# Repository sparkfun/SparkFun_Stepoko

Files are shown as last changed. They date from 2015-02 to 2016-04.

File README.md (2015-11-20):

SparkFun GRBL Board
========================================

SparkFun Stepoko

[*SparkFun Stepoko (ROB-13155)*](https://www.sparkfun.com/products/13155)

A 3 axis motor controller for use with grbl.

Repository Contents (template)
-------------------

* **/Examples** - Example gcode files, projects, and settings
* **/Hardware** - Eagle design files (.brd, .sch)
* **/Mechanical** - Enclosure and heatsink mechanical drawings
* **/Production** - Production panel files (.brd)

Documentation
--------------
* **Hookup Guide** - Basic hookup guide for the Stepoko
* **Coaster Project Tutorial** - Process of creating the coaster example
* **[SparkFun Fritzing repo](https://github.com/sparkfun/Fritzing_Parts)** - Fritzing diagrams for SparkFun products.
* **[SparkFun 3D Model repo](https://github.com/sparkfun/3D_Models)** - 3D models of SparkFun products. 

Product Versions
----------------
[*SparkFun Stepoko (ROB-13155)*](https://www.sparkfun.com/products/13155)

Version History
---------------
* [v1.0](https://github.com/sparkfun/SparkFun_Stepoko/tree/V_1_0) - Released to Reds
* [v1.1](https://github.com/sparkfun/SparkFun_Stepoko/tree/V_1_1) - Changed pot symbol name and 'top-side' resistor value
* [v1.2](https://github.com/sparkfun/SparkFun_Stepoko/tree/V_1_2) - Updated capacitor values, documentation finished

License Information
-------------------

This product is _**open source**_! 

Please review the LICENSE.md file for license information. 

If you have any questions or concerns on licensing, please contact techsupport@sparkfun.com.

Distributed as-is; no warranty is given.

- Your friends at SparkFun.

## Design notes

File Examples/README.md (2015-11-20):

Stepoko Examples
========================================

This directory contains example 3D models, machine code, and settings

Directory Contents
-------------------

* **/BasicShapes** - Example gcode files that drive the mill in 10 inch squares and lines at various speeds
* **/FlameCoaster** - Flat design files and gcode exports for cutting and engraving a SparkFun coaster.
* **/grblSettings** - Example settings for the grbl software; stock Shapeoko, fast Shapeoko, and CDrom steppers.
* **/MidiShieldEnclosure** - 3D models and mill paths to cut a wood enclosure and panel top.

License Information
-------------------

This product is _**open source**_! 

Please review the LICENSE.md file for license information. 

If you have any questions or concerns on licensing, please contact techsupport@sparkfun.com.

Distributed as-is; no warranty is given.

- Your friends at SparkFun.

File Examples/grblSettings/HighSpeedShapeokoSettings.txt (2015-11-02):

(New settings)
$0=30 (step pulse, usec)
$1=255 (step idle delay, msec)
$2=0 (step port invert mask:00000000)
$3=0 (dir port invert mask:00000000)
$4=0 (step enable invert, bool)
$5=0 (limit pins invert, bool)
$6=0 (probe pin invert, bool)
$10=3 (status report mask:00000011)
$11=0.050 (junction deviation, mm)
$12=0.002 (arc tolerance, mm - NEW SETTING)
$13=0 (report inches, bool)
$20=0 (soft limits, bool)
$21=0 (hard limits, bool)
$22=0 (homing cycle, bool)
$23=1 (homing dir invert mask:00000001)
$24=25.000 (homing feed, mm/min)
$25=250.000 (homing seek, mm/min)
$26=100 (homing debounce, msec)
$27=1.000 (homing pull-off, mm)
$100=40 (x, step/mm)
$101=40 (y, step/mm)
$102=40 (z, step/mm)
$110=10000.000 (x max rate, mm/min)
$111=10000.000 (y max rate, mm/min)
$112=1000.000 (z max rate, mm/min)
$120=100.000 (x accel, mm/sec^2)
$121=100.000 (y accel, mm/sec^2)
$122=100.000 (z accel, mm/sec^2)

$130=500.000 (x max travel, mm - NEW SETTING)
$131=500.000 (y max travel, mm - NEW SETTING)
$132=30.000 (z max travel, mm - NEW SETTING)

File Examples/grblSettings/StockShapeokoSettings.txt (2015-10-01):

(New settings)
$0=30 (step pulse, usec)
$1=255 (step idle delay, msec)
$2=0 (step port invert mask:00000000)
$3=0 (dir port invert mask:00000000)
$4=0 (step enable invert, bool)
$5=0 (limit pins invert, bool)
$6=0 (probe pin invert, bool)
$10=3 (status report mask:00000011)
$11=0.050 (junction deviation, mm)
$12=0.002 (arc tolerance, mm - NEW SETTING)
$13=0 (report inches, bool)
$20=0 (soft limits, bool)
$21=0 (hard limits, bool)
$22=0 (homing cycle, bool)
$23=1 (homing dir invert mask:00000001)
$24=25.000 (homing feed, mm/min)
$25=250.000 (homing seek, mm/min)
$26=100 (homing debounce, msec)
$27=1.000 (homing pull-off, mm)
$100=40 (x, step/mm)
$101=40 (y, step/mm)
$102=40 (z, step/mm)
$110=500.000 (x max rate, mm/min)
$111=500.000 (y max rate, mm/min)
$112=500.000 (z max rate, mm/min)
$120=25.000 (x accel, mm/sec^2)
$121=25.000 (y accel, mm/sec^2)
$122=25.000 (z accel, mm/sec^2)
$130=225.000 (x max travel, mm - NEW SETTING)
$131=125.000 (y max travel, mm - NEW SETTING)
$132=170.000 (z max travel, mm - NEW SETTING)

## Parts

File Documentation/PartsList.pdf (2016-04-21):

Deluxe Shapeoko Parts List | Approximate Sizes
Check | Qty. Item description | Metric | Inches
Large:
2 | Waste-boards | 58x36cm | 22x14in
2 | long extrusions/rails, no tap holes | 60cm | 24in
1 | long extrusion/rails, two tapped holes | 60cm | 24in

Red Plates:
2 | “L” shaped base ends | 72cm | 28in
1 | “I” shape (Cross strap, for sub base) | 68cm | 27in
1 | center strap, 4 slotted holes | 58cm | 22in
2 | side strap, 2 holes | 58cm | 22in
1 | moving Z axis plate, 2 tabs | 18x16cm | 7x6in
1 | 25x17cm | 10x7in
2 | 21x16cm | 8x6in

Electronics:
4 | Wantai stepper motors (NEMA 23)
1 | 1x Stepoko controller board
1 | 1x usb cable
1 | 1x SPST toggle
1 | 1x IEC power cord, US
1 | 1x power supply brick

Misc HW:
1 | 1DPN611 spindle mount | 10x9x3cm | 4x4x1in
2 | extrusions with 45deg rail, z axis rails | 20x2x2.7cm 8x1x1in
1 | red plastic enclosure with pre-milled holes
1 | red plastic enclosure lid
1 | Shapeoko placard
2 | expansion springs | 5.5cm | 2in
6 | Belt clips, angle with two slots and two holes
10 | 3M Bump-on rubber bumpers
1 | 10mm open end wrench
1 | 8mm open end wrench
1 | 13mm open end wrench
5 | Allen hex keys
1 | Tube thread-locker (jet-lube branding)
1 | Sharpie
1 | Thermal gap filler pad | 7.5x10cm | 3x4 in
3 | cable carriers | 1x1.5x50cm ~20 in

Spacers and Stand-Offs:
2 | 10-24 x 1 inch, threaded | 2.5cm | 1in
4 | 9mm O.D, 1-1/4 inch long | 1 ¼ in
4 | 3/8in O.D., .219in I.D, by 3/8in | 3/8 in
1 | 3/8in O.D., .219in I.D,by 5/16in | 5/16 in
2 | M5 x 15mm threaded | 1.5cm | 0.6 in
6 | 0.5in O.D., 0.319 I.D, x10mm | 1cm | 0.4 in

fixed Z axis plate (moves with Y axis), centered large motor hole
Y axis end plates, offset motor hole. (Moves with X axis)

Belts:
3 | Split belts (GT2, 800mm) | 80cm | 31.5 in
1 | Continuous belt (GT2, 524mm) | 52.4cm | 20.6 in

Pulleys:
4 | 6.3mm bore (GT2 profile)
1 | 5mm bore (GT2 profile)
10 | (or more) set screws for pulleys

Bolts/screws:
6 | M8 x 35mm | 35mm | 1.4 in
30 | M6 x 12mm | 12mm | 0.47 in
1 | M6 x 30mm | 30mm | 1.2 in
25 | M5 x 16mm | 16mm | 0.63 in
22 | M5 x 20mm | 20mm | 0.79 in
2 | M5 x 55, cylindrical hex cap (SHCS) | 55mm | 2.16 in
4 | M5 x 40mm | 40mm | 1.6 in
1 | M5 x 25mm | 25mm | 1 in
2 | 10-24 thread, 3/4inch | 19mm | 0.75 in
12 | M3 x 12mm gnarled hex cap (SHCS) | 12mm | 0.5 in
6 | 6-32 x 3/4in for red enclosure lid | 19mm | 0.75 in
8 | 4-40 x 3/8in for PCB mounting | 9mm | 0.375 in

Nuts:
6 | M8 Hex Nut
1 | M6 x 6mm Hex Nut
4 | M6 Square Nut
29 | M5 Hex Nut
8 | Hex Nut with eccentric hole and shoulder
12 | M3 Hex Nut

Washers:
4 | M6 Flat Washer
18 | M5 Flat Washer

Bearings:
16 | Black V-guide pulleys
12 | 25mm outside diameter(8x22x7mm) | 1 in
2 | 14mm outside diameter (6mm flanged bearing) | 0.5 in

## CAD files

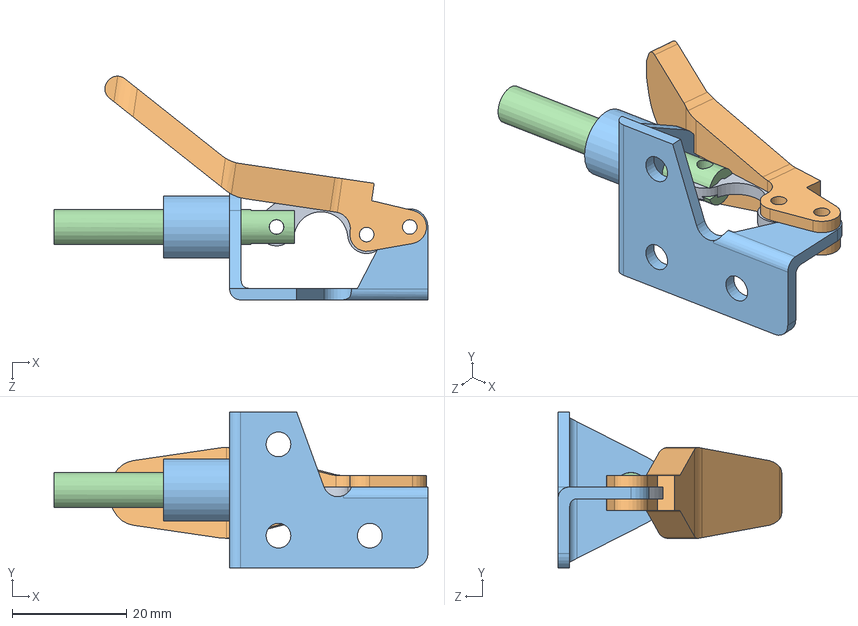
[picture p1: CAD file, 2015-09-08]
Mechanical/HeatsinkJig/ToggleClamp.SLDASM
65.1 x 27.2 x 39.0 mm
ToggleClampConnector
ToggleClampLever
toggleClampMount
ToggleClampPlunger

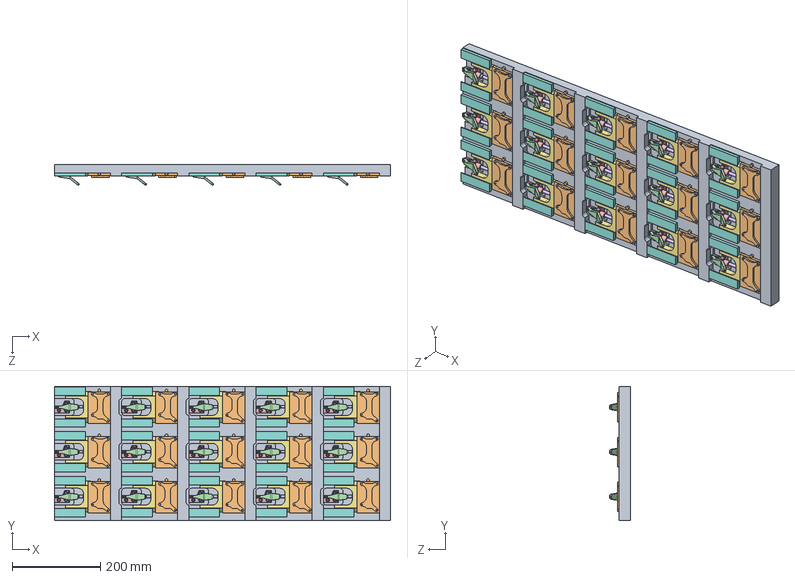
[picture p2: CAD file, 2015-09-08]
Mechanical/HeatsinkJig/HeatSinkJig.SLDASM
762.0 x 304.8 x 46.6 mm
JigBase
HeatSink x 15
ToggleClampConnector x 15
ToggleClampLever x 15
toggleClampMount x 15
ToggleClampPlunger x 15
JigClampFace x 15
dovetail x 30
socket head cap screw_ai x 46
rollpin x 15

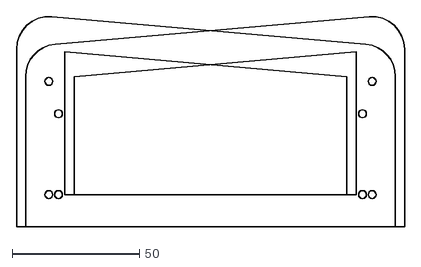
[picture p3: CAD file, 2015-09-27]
Examples/MidiShieldEnclosure/Controlled/dxf/SideParts.dxf
152.4 x 82.8

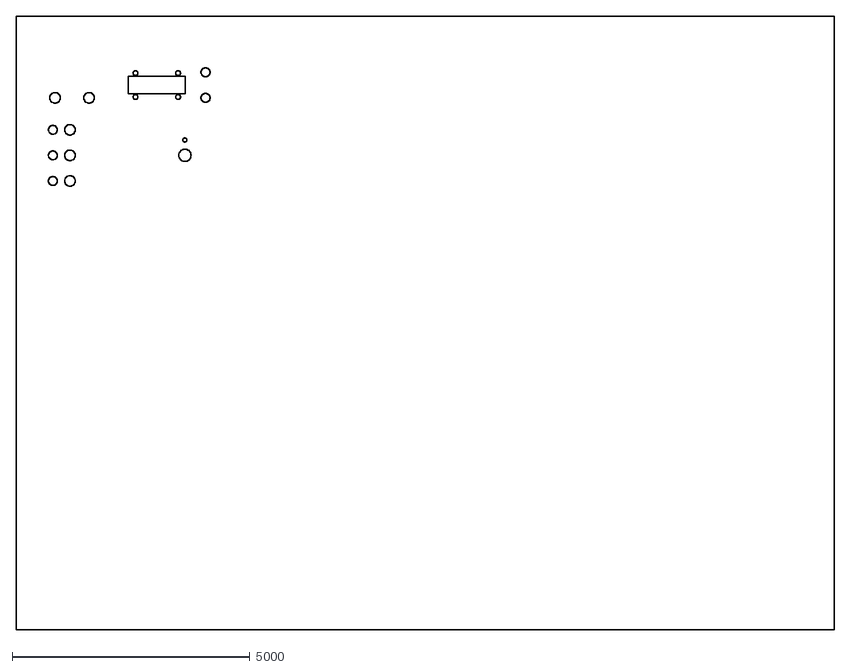
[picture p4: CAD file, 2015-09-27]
Examples/MidiShieldEnclosure/PanelExports/panel_holes.dxf
17204.3 x 12903.2

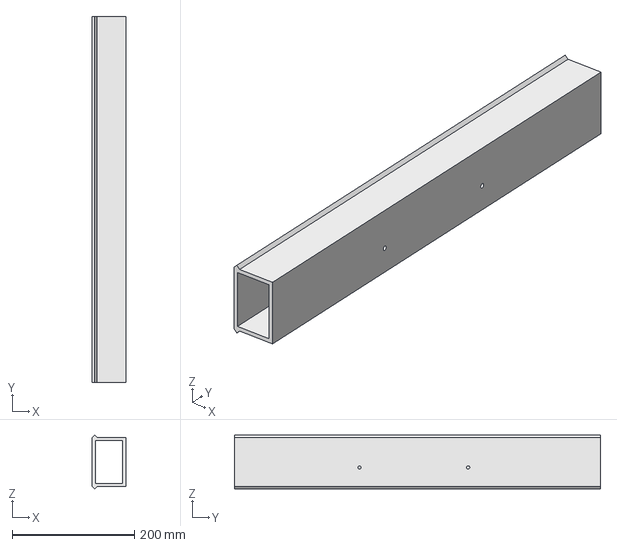
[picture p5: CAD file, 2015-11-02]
Mechanical/ChassisMount/RailPart.FCStd
55.0 x 600.0 x 88.0 mm

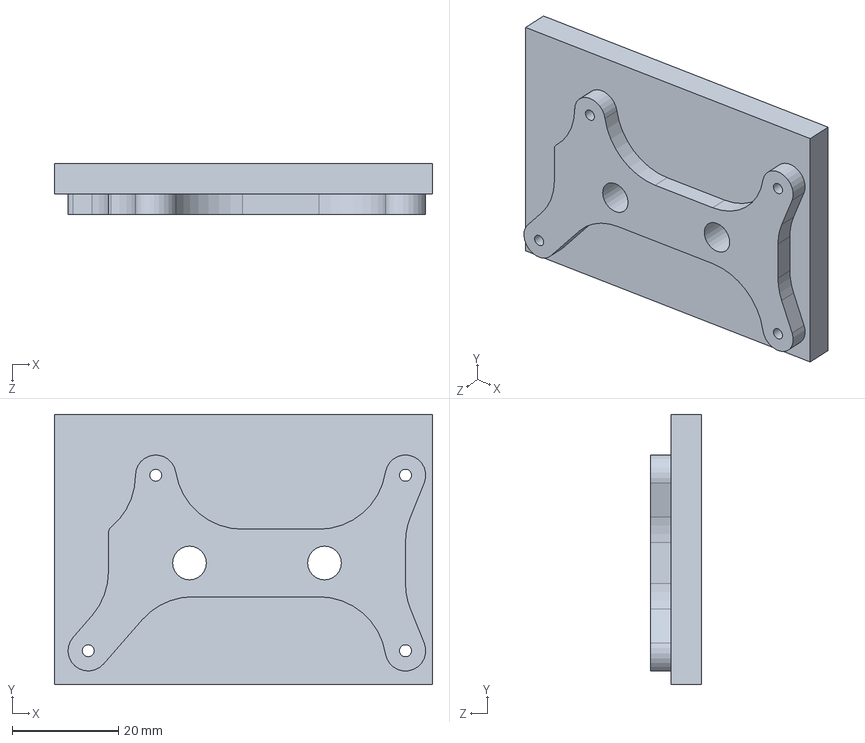
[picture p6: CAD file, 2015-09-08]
Mechanical/HeatSink.SLDPRT
71.1 x 50.8 x 9.53 mm

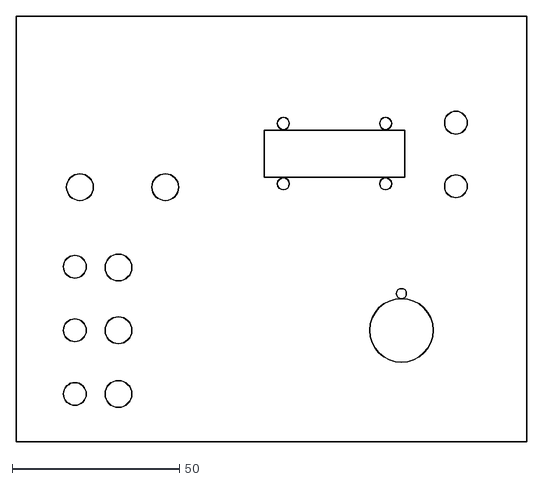
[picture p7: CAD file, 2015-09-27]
Examples/MidiShieldEnclosure/PanelExports/freecadexport.dxf
152.4 x 127.0

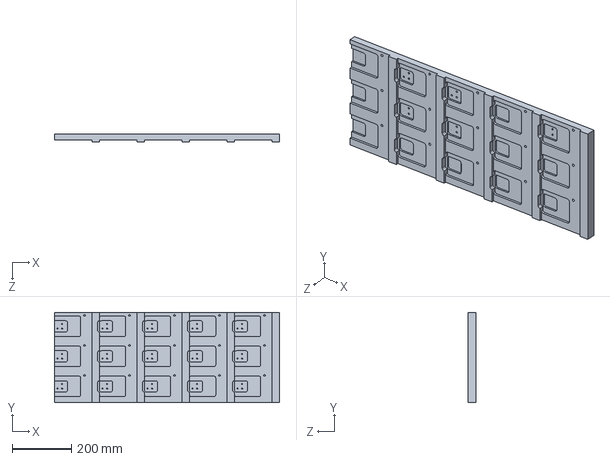
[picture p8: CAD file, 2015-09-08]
Mechanical/HeatsinkJig/JigBase.SLDPRT
762.0 x 304.8 x 25.4 mm

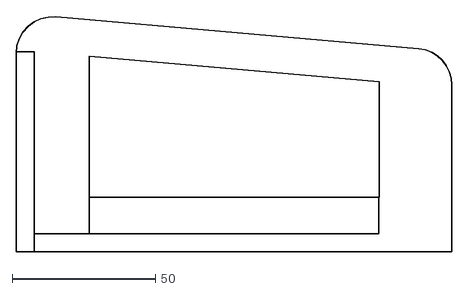
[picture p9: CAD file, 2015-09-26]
Examples/MidiShieldEnclosure/PanelTestMaster.dxf
151.9 x 82.3

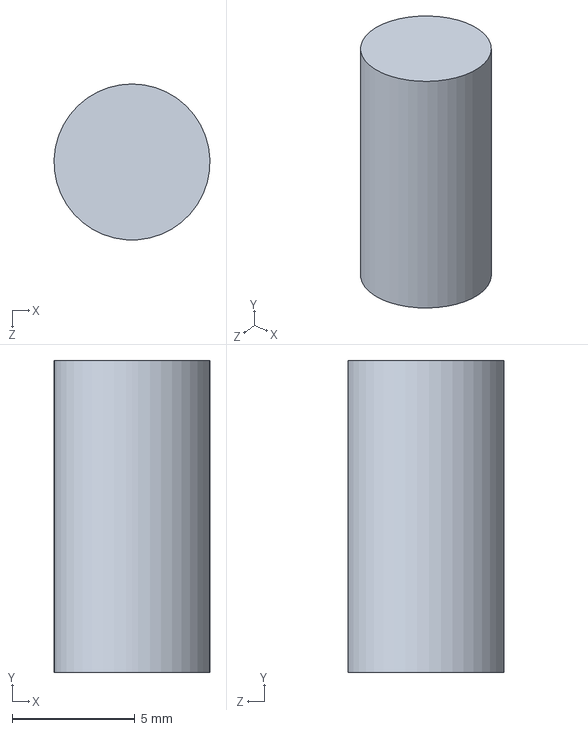
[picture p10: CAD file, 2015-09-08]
Mechanical/HeatsinkJig/rollpin.SLDPRT
6.35 x 12.7 x 6.35 mm

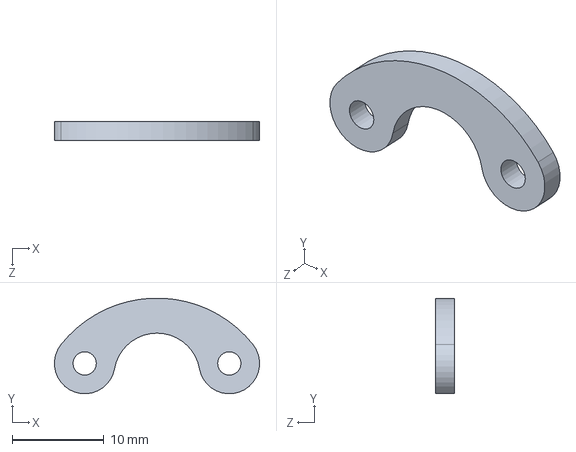
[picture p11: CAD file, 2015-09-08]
Mechanical/HeatsinkJig/ToggleClampConnector.SLDPRT
22.3 x 10.4 x 2.03 mm

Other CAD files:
Examples/MidiShieldEnclosure/Components.FCStd
Examples/MidiShieldEnclosure/Controlled/FrontPart.FCStd
Examples/MidiShieldEnclosure/Controlled/PanelPart.FCStd
Examples/MidiShieldEnclosure/TopPanel.FCStd
Examples/MidiShieldEnclosure/Controlled/BottomPart.FCStd
Examples/MidiShieldEnclosure/Controlled/BackPart.FCStd
Examples/MidiShieldEnclosure/Controlled/SideView.FCStd
Examples/MidiShieldEnclosure/Controlled/dxf/BackPart.dxf
Examples/MidiShieldEnclosure/Controlled/dxf/BottomPart.dxf
Examples/MidiShieldEnclosure/Controlled/dxf/FrontPart.dxf
Examples/MidiShieldEnclosure/Controlled/dxf/PanelPart.dxf
Mechanical/HeatsinkJig/JigClampFace.SLDPRT
Mechanical/HeatsinkJig/ToggleClampLever.SLDPRT
Mechanical/HeatsinkJig/ToggleClampPlunger.SLDPRT
Mechanical/HeatsinkJig/dovetail.SLDPRT
Mechanical/HeatsinkJig/toggleClampMount.SLDPRT

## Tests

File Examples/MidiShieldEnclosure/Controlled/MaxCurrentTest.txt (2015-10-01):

10,23.50,24.25,24.00,23.50
15,23.50,24.25,24.25,23.50
20,23.50,24.50,24.25,23.50
25,23.50,24.25,24.00,23.50
30,23.50,24.25,24.00,23.50
35,23.50,24.25,24.00,23.75
40,23.50,24.25,24.00,23.75
45,23.50,24.25,24.00,23.50
50,23.50,24.25,24.00,23.50
55,23.50,24.25,24.00,23.50
60,23.50,24.25,24.00,23.50
65,23.50,24.50,24.00,23.50
70,23.50,24.25,24.00,23.50
75,23.50,24.50,24.00,23.50
80,23.50,24.25,24.25,23.50
85,23.50,24.25,24.00,23.50
90,23.50,24.25,24.00,23.50
95,23.50,24.50,24.00,23.50
100,23.50,24.25,24.00,23.50
105,23.50,24.25,24.00,23.50
110,23.50,24.25,24.00,23.50
115,23.25,24.25,24.00,23.75
120,23.50,24.25,24.00,23.50
125,23.50,24.25,23.50,23.50
130,23.50,24.25,24.00,23.50
135,23.50,24.25,24.00,23.50
140,
MAX31855K::SCG Fault: Thermocouple is shorted to GND
24.25,23.75,23.50
145,11.50,24.50,24.25,23.75
150,12.25,24.75,24.50,26.00
155,9.50,24.75,24.75,31.50
160,
MAX31855K::SCG Fault: Thermocouple is shorted to GND
25.00,25.00,29.50
165,12.00,25.00,26.00,27.50
170,14.50,25.00,29.50,26.25
175,
MAX31855K::SCG Fault: Thermocouple is shorted to GND
28.25,29.75,25.75
180,
MAX31855K::SCV Fault: Thermocouple is shorted to VCC
32.50,29.50,25.25
185,26.25,32.50,29.50,25.25
190,26.75,30.50,29.50,30.50
195,
MAX31855K::SCV Fault: Thermocouple is shorted to VCC
29.00,29.50,35.75
200,
MAX31855K::SCV Fault: Thermocouple is shorted to VCC
28.00,29.50,39.00
205,27.00,27.25,29.50,41.25
210,
MAX31855K::SCG Fault: Thermocouple is shorted to GND
27.00,29.50,42.75
215,27.50,26.50,29.50,43.75
220,
MAX31855K::SCG Fault: Thermocouple is shorted to GND
26.50,29.75,44.50
225,27.75,26.25,30.25,45.25
230,27.75,26.25,29.75,45.50
235,28.00,26.25,30.25,45.75
240,27.75,26.50,30.25,45.75
245,28.00,26.50,30.75,46.25
250,
MAX31855K::SCV Fault: Thermocouple is shorted to VCC
26.50,30.75,41.00
255,
MAX31855K::SCG Fault: Thermocouple is shorted to GND
26.50,31.00,35.50
260,24.00,26.75,30.75,32.00
265,25.00,26.75,30.75,29.75
270,24.75,26.75,30.75,28.50
275,23.50,26.75,30.75,27.50
280,
MAX31855K::SCG Fault: Thermocouple is shorted to GND
26.75,30.50,26.75
285,24.00,26.75,30.25,26.25
290,
MAX31855K::SCG Fault: Thermocouple is shorted to GND
26.75,30.50,26.00
295,23.75,26.50,30.25,26.00
300,
MAX31855K::SCG Fault: Thermocouple is shorted to GND
26.50,30.25,25.75
305,23.25,26.25,30.25,25.75
310,23.50,26.25,30.00,25.50
315,
MAX31855K::SCG Fault: Thermocouple is shorted to GND
26.25,30.00,25.50
320,23.50,26.00,30.25,25.50
325,
MAX31855K::SCV Fault: Thermocouple is shorted to VCC
26.25,30.25,25.25
330,23.25,26.25,30.00,25.25
335,
MAX31855K::SCG Fault: Thermocouple is shorted to GND
26.25,30.00,25.25
340,24.25,26.25,30.00,25.25
345,23.25,26.25,30.00,25.25
350,
MAX31855K::SCG Fault: Thermocouple is shorted to GND
26.00,30.00,25.25
355,23.50,26.00,30.00,25.25
360,
MAX31855K::SCG Fault: Thermocouple is shorted to GND
26.00,29.75,25.25
365,
MAX31855K::SCG Fault: Thermocouple is shorted to GND
26.00,30.00,25.00
370,23.25,25.75,29.75,25.00
375,22.75,26.00,30.00,25.00
380,
MAX31855K::SCV Fault: Thermocouple is shorted to VCC
26.00,29.75,25.25
385,23.25,25.75,29.75,25.00
390,
MAX31855K::SCV Fault: Thermocouple is shorted to VCC
25.75,29.75,25.00
395,
MAX31855K::SCG Fault: Thermocouple is shorted to GND
26.00,30.00,25.00
400,23.00,26.00,29.75,25.00
405,
MAX31855K::SCG Fault: Thermocouple is shorted to GND
25.75,29.75,25.00
410,23.25,25.75,29.75,25.00
415,
MAX31855K::SCG Fault: Thermocouple is shorted to GND
25.75,29.75,24.75
420,
MAX31855K::SCV Fault: Thermocouple is shorted to VCC
25.75,29.75,25.00
425,
MAX31855K::SCG Fault: Thermocouple is shorted to GND
25.75,29.75,25.00
430,23.25,25.75,29.75,25.00
435,
MAX31855K::SCV Fault: Thermocouple is shorted to VCC
25.75,29.50,25.00
440,
MAX31855K::SCV Fault: Thermocouple is shorted to VCC
25.50,29.50,25.00
445,
MAX31855K::SCG Fault: Thermocouple is shorted to GND
25.75,29.50,24.75
450,
MAX31855K::SCG Fault: Thermocouple is shorted to GND
25.75,29.75,24.75
455,22.75,25.75,29.75,24.75
460,23.00,25.75,29.50,24.75
465,
MAX31855K::SCG Fault: Thermocouple is shorted to GND
25.75,29.50,24.75
470,23.00,25.75,29.75,25.00
475,
MAX31855K::SCG Fault: Thermocouple is shorted to GND
25.75,29.50,24.75
480,
MAX31855K::SCG Fault: Thermocouple is shorted to GND
25.75,29.75,24.75
485,22.50,25.75,29.75,24.75
490,23.00,25.75,29.50,24.75
495,
MAX31855K::SCG Fault: Thermocouple is shorted to GND
25.75,29.75,24.75
500,
MAX31855K::SCG Fault: Thermocouple is shorted to GND
25.75,29.75,24.75
505,23.00,25.75,29.50,24.75
510,23.00,25.50,29.50,24.75
515,23.25,25.75,29.50,24.75
520,22.75,25.75,29.75,24.75
525,22.50,25.75,29.75,24.75
530,
MAX31855K::SCV Fault: Thermocouple is shorted to VCC
25.75,29.75,24.75
535,22.75,25.75,29.50,24.75
540,22.75,25.75,29.50,24.75
545,22.75,25.75,29.75,24.75
550,
MAX31855K::SCG Fault: Thermocouple is shorted to GND
25.50,29.75,25.00
555,
MAX31855K::SCG Fault: Thermocouple is shorted to GND
25.75,29.75,24.75
560,
MAX31855K::SCG Fault: Thermocouple is shorted to GND
25.50,29.50,25.00
565,22.75,25.75,29.50,24.75
570,
MAX31855K::SCG Fault: Thermocouple is shorted to GND
25.50,29.75,24.75
575,23.00,25.50,29.75,24.75
580,22.75,25.75,29.50,24.75
585,23.25,25.75,29.50,24.75
590,23.25,25.75,29.75,24.75
595,23.00,25.75,29.75,24.75
600,
MAX31855K::SCV Fault: Thermocouple is shorted to VCC
25.75,29.75,24.75
605,
MAX31855K::SCG Fault: Thermocouple is shorted to GND
25.75,29.75,24.75
610,23.00,25.75,29.50,24.75
615,
MAX31855K::SCG Fault: Thermocouple is shorted to GND
25.75,29.50,24.75
620,
MAX31855K::SCV Fault: Thermocouple is shorted to VCC
25.75,29.75,24.75
625,23.00,25.50,29.50,25.00
630,23.00,25.50,29.75,25.00
635,22.75,25.50,29.50,25.00
640,23.00,25.50,29.50,25.00
645,22.50,25.50,29.75,24.75
650,
MAX31855K::SCG Fault: Thermocouple is shorted to GND
25.50,29.75,24.75
655,22.75,25.50,29.75,24.75
660,22.50,25.75,29.50,24.75
665,23.50,25.75,29.75,25.00
670,
MAX31855K::SCV Fault: Thermocouple is shorted to VCC
25.50,29.50,25.00
675,
MAX31855K::SCG Fault: Thermocouple is shorted to GND
25.75,29.75,24.75
680,23.25,25.75,29.50,25.00
685,22.75,25.75,29.50,24.75
690,
MAX31855K::SCV Fault: Thermocouple is shorted to VCC
25.50,29.50,24.75
695,23.00,25.75,29.50,24.75
700,23.00,25.75,29.50,24.75
705,23.00,25.75,29.75,25.00
710,23.00,25.50,29.75,24.75
715,
MAX31855K::SCG Fault: Thermocouple is shorted to GND
25.50,29.50,25.00
720,23.00,25.50,29.75,24.75
725,
MAX31855K::SCG Fault: Thermocouple is shorted to GND
25.75,29.75,24.75
730,
MAX31855K::SCG Fault: Thermocouple is shorted to GND
25.75,29.50,24.75
735,
MAX31855K::SCV Fault: Thermocouple is shorted to VCC
25.75,29.50,24.75
740,
MAX31855K::SCV Fault: Thermocouple is shorted to VCC
25.75,29.50,24.75
745,
MAX31855K::SCV Fault: Thermocouple is shorted to VCC
25.75,29.50,25.00
750,
MAX31855K::SCG Fault: Thermocouple is shorted to GND
25.50,29.50,25.00
755,
MAX31855K::SCG Fault: Thermocouple is shorted to GND
25.75,29.75,25.00
760,
MAX31855K::SCG Fault: Thermocouple is shorted to GND
25.75,29.50,25.00
765,
MAX31855K::SCG Fault: Thermocouple is shorted to GND
25.50,29.50,25.00
770,23.25,25.50,29.50,24.75
775,
MAX31855K::SCV Fault: Thermocouple is shorted to VCC
25.75,29.75,24.75
780,
MAX31855K::SCG Fault: Thermocouple is shorted to GND
25.75,29.50,24.75
785,22.75,25.50,29.50,24.75
790,
MAX31855K::SCG Fault: Thermocouple is shorted to GND
25.75,29.50,25.00
795,23.25,25.75,29.50,24.75
800,
MAX31855K::SCV Fault: Thermocouple is shorted to VCC
25.75,29.75,25.00
805,22.75,25.75,29.75,24.75
810,
MAX31855K::SCG Fault: Thermocouple is shorted to GND
25.75,29.50,25.00
815,22.75,25.50,29.50,24.75
820,22.50,25.75,29.50,24.75
825,22.50,25.75,29.50,24.75
830,22.75,25.50,29.50,25.00
835,22.75,25.50,29.50,25.00
840,
MAX31855K::SCV Fault: Thermocouple is shorted to VCC
25.50,29.50,24.75
845,22.75,25.50,29.75,25.00
850,22.25,25.50,29.50,24.75
855,23.25,25.75,29.50,24.75
860,
MAX31855K::SCG Fault: Thermocouple is shorted to GND
25.75,29.50,24.75
865,23.00,25.75,29.50,24.75
870,
MAX31855K::SCG Fault: Thermocouple is shorted to GND
25.75,29.50,25.00
875,23.00,25.75,29.50,25.00
880,22.75,25.75,29.50,24.75
885,
MAX31855K::SCV Fault: Thermocouple is shorted to VCC
25.75,29.50,24.75
890,22.50,25.75,29.50,24.75
895,22.75,25.75,29.50,24.75
900,
MAX31855K::SCG Fault: Thermocouple is shorted to GND
25.50,29.50,24.75
905,
MAX31855K::SCG Fault: Thermocouple is shorted to GND
25.50,29.50,24.75
910,22.75,25.50,29.50,25.00
915,
MAX31855K::SCV Fault: Thermocouple is shorted to VCC
25.50,29.50,25.00
920,
MAX31855K::SCG Fault: Thermocouple is shorted to GND
25.75,29.50,25.00
925,22.00,25.75,29.50,
MAX31855K::SCG Fault: Thermocouple is shorted to GND
930,
MAX31855K::SCG Fault: Thermocouple is shorted to GND
25.75,29.50,24.75
935,
MAX31855K::SCG Fault: Thermocouple is shorted to GND
25.75,29.50,24.75
940,22.25,25.75,29.50,24.75
945,22.75,25.75,29.50,24.75
950,22.75,25.75,29.75,25.00
955,22.25,25.75,29.50,25.00
960,
MAX31855K::SCV Fault: Thermocouple is shorted to VCC
25.75,29.50,25.00
965,
MAX31855K::SCG Fault: Thermocouple is shorted to GND
25.50,29.50,25.00
970,22.25,25.75,29.50,24.75
975,
MAX31855K::SCG Fault: Thermocouple is shorted to GND
25.75,29.75,24.75
980,22.75,25.50,29.50,24.75
985,22.25,25.50,29.50,24.75
990,
MAX31855K::SCG Fault: Thermocouple is shorted to GND
25.75,29.50,25.00
995,24.50,25.75,29.50,25.00
1000,24.25,25.50,28.25,24.75
1005,24.25,25.50,27.25,24.75
1010,24.25,25.50,26.50,24.50
1015,24.00,25.25,26.00,24.75
1020,24.00,25.25,25.75,24.50
1025,24.25,25.25,25.50,24.50
1030,24.25,25.25,25.25,24.50
1035,23.50,25.00,25.00,24.25
1040,23.50,25.00,25.00,24.25
1045,23.50,25.00,25.00,24.25
1050,23.50,24.75,24.75,24.25
1055,23.50,25.00,24.75,24.25
1060,23.50,24.75,24.75,24.00
1065,23.50,24.75,24.75,24.00
1070,23.50,24.75,24.75,24.25
1075,23.50,24.75,24.75,24.25
1080,23.50,24.75,24.75,24.25
1085,23.50,24.75,24.50,24.25
1090,23.50,25.00,24.50,24.25
1095,23.50,24.75,24.50,24.00
1100,23.50,24.75,24.50,24.00
1105,23.25,24.50,24.50,24.00
1110,23.25,24.75,24.25,23.75
1115,23.25,24.75,24.50,24.00
1120,23.25,24.50,24.50,24.00
1125,23.25,24.75,24.50,24.00
1130,23.25,24.75,24.25,24.00
1135,23.25,24.75,24.50,23.75
1140,23.25,24.75,24.50,24.00
1145,23.25,24.75,24.50,24.00
1150,23.25,24.75,24.25,24.00
1155,23.25,24.75,24.50,24.00
1160,23.25,24.75,24.50,23.75
1165,23.25,24.75,24.50,24.00
1170,23.25,24.75,24.25,24.00
1175,23.25,24.50,24.50,23.75
1180,23.25,24.50,24.50,24.00
1185,23.25,24.50,24.25,23.75
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
MAX31855K::SCG Fault: Thermocouple is shorted to GND
25.00,26.25,24.25
1350,22.75,25.00,27.25,29.25
1355,
MAX31855K::SCG Fault: Thermocouple is shorted to GND
25.00,28.00,28.50
1360,
MAX31855K::SCV Fault: Thermocouple is shorted to VCC
25.00,28.25,27.25
1365,
MAX31855K::SCG Fault: Thermocouple is shorted to GND
25.25,28.50,26.25
1370,22.50,25.25,28.75,25.75
1375,
MAX31855K::SCG Fault: Thermocouple is shorted to GND
25.25,29.00,25.25
1380,
MAX31855K::SCG Fault: Thermocouple is shorted to GND
25.25,29.00,25.00
1385,
MAX31855K::SCG Fault: Thermocouple is shorted to GND
25.25,29.25,25.00
1390,23.00,25.50,29.00,25.00
1395,23.00,25.50,29.25,25.00
1400,
MAX31855K::SCG Fault: Thermocouple is shorted to GND
25.50,29.25,25.00
1405,
MAX31855K::SCG Fault: Thermocouple is shorted to GND
25.50,29.25,25.00
1410,
MAX31855K::SCG Fault: Thermocouple is shorted to GND
25.75,29.25,25.00
1415,
MAX31855K::SCG Fault: Thermocouple is shorted to GND
25.75,29.50,24.75
1420,
MAX31855K::SCG Fault: Thermocouple is shorted to GND
25.75,29.50,25.00
1425,
MAX31855K::SCV Fault: Thermocouple is shorted to VCC
25.75,29.50,25.00
1430,
MAX31855K::SCG Fault: Thermocouple is shorted to GND
25.50,29.75,25.00
1435,
MAX31855K::SCV Fault: Thermocouple is shorted to VCC
25.75,29.50,25.00
1440,
MAX31855K::SCG Fault: Thermocouple is shorted to GND
25.75,29.50,25.00
1445,
MAX31855K::SCG Fault: Thermocouple is shorted to GND
25.50,29.75,25.00
1450,
MAX31855K::SCG Fault: Thermocouple is shorted to GND
25.75,29.75,25.00
1455,22.75,25.75,29.75,25.00
1460,
MAX31855K::SCG Fault: Thermocouple is shorted to GND
25.75,29.75,25.00
1465,23.25,25.50,29.50,25.00
1470,22.50,25.75,29.75,25.00
1475,13.50,26.00,31.50,25.25
1480,
MAX31855K::SCG Fault: Thermocouple is shorted to GND
30.75,35.50,25.75
1485,
MAX31855K::SCG Fault: Thermocouple is shorted to GND
34.75,38.75,31.50
1490,
MAX31855K::SCG Fault: Thermocouple is shorted to GND
37.75,41.25,36.25
1495,
MAX31855K::SCG Fault: Thermocouple is shorted to GND
40.00,43.25,39.50
1500,17.25,41.50,44.50,41.75
1505,18.25,42.75,45.50,43.25
1510,19.25,43.75,46.25,44.50
1515,
MAX31855K::SCG Fault: Thermocouple is shorted to GND
42.50,45.25,43.00
1520,
MAX31855K::SCV Fault: Thermocouple is shorted to VCC
43.50,45.75,44.25
1525,
MAX31855K::SCG Fault: Thermocouple is shorted to GND
44.50,46.75,45.50
1530,18.75,45.50,47.50,46.00
1535,19.00,43.00,45.25,42.75
1540,18.75,43.75,45.50,44.00
1545,19.00,44.75,46.75,45.25
1550,24.25,45.75,48.00,46.00
1555,14.50,46.50,49.00,46.75
1560,
MAX31855K::SCG Fault: Thermocouple is shorted to GND
46.75,49.25,47.25
1565,24.75,47.00,50.00,47.50
1570,19.00,47.50,50.50,47.75
1575,16.75,47.75,50.50,48.00
1580,20.00,48.00,50.75,48.25
1585,25.25,48.25,51.00,48.25
1590,16.25,48.50,51.25,48.50
1595,16.00,48.50,51.50,48.75
1600,25.25,48.75,51.75,48.75
1605,
MAX31855K::SCG Fault: Thermocouple is shorted to GND
49.00,52.00,49.00
1610,
MAX31855K::SCG Fault: Thermocouple is shorted to GND
49.00,52.00,49.25
1615,
MAX31855K::SCG Fault: Thermocouple is shorted to GND
49.00,51.75,49.00
1620,15.75,49.00,52.00,49.25
1625,16.25,49.00,52.00,49.25
1630,16.75,49.00,52.00,49.50
1635,16.75,49.25,52.00,49.75
1640,16.75,49.25,52.00,49.75
1645,16.00,49.25,52.00,49.75
1650,27.25,49.50,52.00,49.75
1655,20.75,49.50,52.25,50.00
1660,26.25,49.75,52.50,50.00
1665,16.75,49.75,52.75,50.00
1670,17.00,49.75,52.75,50.00
1675,21.00,50.00,53.00,50.25
1680,27.00,50.00,53.25,50.25
1685,27.25,50.25,53.25,50.25
1690,21.25,50.25,53.00,50.25
1695,27.00,50.25,53.25,50.25
1700,
MAX31855K::SCG Fault: Thermocouple is shorted to GND
50.25,53.25,50.25
1705,
MAX31855K::SCV Fault: Thermocouple is shorted to VCC
50.25,53.50,50.50
1710,24.00,50.25,53.75,50.50
1715,22.25,50.50,53.75,50.50
1720,17.00,50.75,53.75,50.50
1725,17.50,50.50,53.50,50.75
1730,
MAX31855K::SCG Fault: Thermocouple is shorted to GND
50.50,53.50,50.75
1735,17.25,50.50,53.25,50.75
1740,
MAX31855K::SCG Fault: Thermocouple is shorted to GND
50.50,53.50,50.75
1745,17.50,50.50,53.50,50.75
1750,25.75,50.75,53.50,50.75
1755,
MAX31855K::SCG Fault: Thermocouple is shorted to GND
51.75,53.50,51.00
1760,26.00,52.75,53.50,51.00
1765,
MAX31855K::SCG Fault: Thermocouple is shorted to GND
53.25,53.50,51.25
1770,
MAX31855K::SCG Fault: Thermocouple is shorted to GND
53.50,53.50,51.00
1775,25.25,54.00,53.75,51.00
1780,26.00,54.25,53.75,51.25
1785,
MAX31855K::SCV Fault: Thermocouple is shorted to VCC
54.25,53.75,51.25
1790,
MAX31855K::SCV Fault: Thermocouple is shorted to VCC
54.50,53.75,51.25
1795,25.75,54.75,53.75,51.25
1800,
MAX31855K::SCV Fault: Thermocouple is shorted to VCC
54.75,53.75,51.50
1805,
MAX31855K::SCG Fault: Thermocouple is shorted to GND
55.00,54.00,51.25
1810,25.50,55.00,54.00,51.50
1815,
MAX31855K::SCV Fault: Thermocouple is shorted to VCC
55.25,54.00,51.50
1820,26.25,55.00,54.00,51.50
1825,
MAX31855K::SCG Fault: Thermocouple is shorted to GND
55.00,54.00,51.50
1830,25.75,55.25,54.25,51.75
1835,25.75,55.00,54.25,51.75
1840,
MAX31855K::SCG Fault: Thermocouple is shorted to GND
55.00,54.25,51.75
1845,
MAX31855K::SCG Fault: Thermocouple is shorted to GND
55.25,54.25,51.75
1850,25.75,55.25,54.25,51.75
1855,26.00,55.00,54.25,51.75
1860,24.25,55.50,54.50,52.00
1865,
MAX31855K::SCG Fault: Thermocouple is shorted to GND
54.75,54.50,51.75
1870,29.25,54.00,54.50,52.00
1875,
MAX31855K::SCG Fault: Thermocouple is shorted to GND
53.50,54.50,52.00
1880,29.00,53.25,54.50,52.00
1885,28.75,53.00,54.75,52.00
1890,28.75,52.75,54.50,52.25
1895,
MAX31855K::SCV Fault: Thermocouple is shorted to VCC
52.50,54.50,52.00
1900,19.00,52.50,54.50,52.25
1905,27.25,52.50,54.50,52.25
1910,28.25,52.50,54.75,52.25
1915,28.75,52.50,54.75,52.25
1920,28.50,52.50,54.75,52.25
1925,28.75,52.50,54.75,52.25
1930,28.75,52.50,54.75,52.25
1935,29.00,52.50,54.75,52.25
1940,25.50,52.50,54.75,52.25
1945,24.25,52.50,54.75,52.25
1950,28.75,52.50,54.75,52.25
1955,29.25,52.50,54.75,52.50
1960,29.25,52.50,54.75,52.50
1965,29.50,52.50,54.75,52.50
1970,29.00,52.50,54.75,52.25
1975,29.25,52.50,54.75,52.50
1980,
MAX31855K::SCG Fault: Thermocouple is shorted to GND
52.75,55.00,52.50
1985,24.00,52.75,54.75,52.50
1990,
MAX31855K::SCV Fault: Thermocouple is shorted to VCC
52.75,55.00,52.50
1995,29.25,52.75,55.00,52.50
2000,32.50,52.75,55.00,52.50
2005,33.00,52.75,54.75,52.50
2010,
MAX31855K::SCV Fault: Thermocouple is shorted to VCC
52.75,55.00,52.50
2015,
MAX31855K::SCG Fault: Thermocouple is shorted to GND
52.75,55.00,52.75
2020,33.00,52.75,55.00,52.50
2025,33.25,52.75,55.25,52.50
2030,
MAX31855K::SCG Fault: Thermocouple is shorted to GND
52.75,55.00,52.75
2035,33.25,52.75,55.00,52.75
2040,
MAX31855K::SCG Fault: Thermocouple is shorted to GND
53.00,55.00,52.75
2045,
MAX31855K::SCG Fault: Thermocouple is shorted to GND
53.00,55.25,52.75
2050,33.00,53.00,55.25,52.75
2055,33.25,53.00,55.00,52.75
2060,33.25,53.00,55.00,52.75
2065,
MAX31855K::SCV Fault: Thermocouple is shorted to VCC
53.00,55.25,52.75
2070,33.00,53.00,55.25,52.75
2075,
MAX31855K::SCG Fault: Thermocouple is shorted to GND
53.00,55.25,52.75
2080,33.00,53.00,55.25,53.00
2085,33.25,53.00,55.25,52.75
2090,33.25,53.00,55.25,52.75
2095,33.25,53.25,55.50,52.75
2100,33.25,53.25,55.25,53.00
2105,
MAX31855K::SCG Fault: Thermocouple is shorted to GND
53.25,55.50,53.00
2110,33.25,53.25,55.50,53.00
2115,33.00,53.25,55.50,53.00
2120,
MAX31855K::SCV Fault: Thermocouple is shorted to VCC
53.25,55.75,53.00
2125,33.50,53.25,55.50,53.00
2130,
MAX31855K::SCG Fault: Thermocouple is shorted to GND
53.25,55.50,53.00
2135,
MAX31855K::SCG Fault: Thermocouple is shorted to GND
53.25,55.50,53.00
2140,33.50,53.25,55.50,53.00
2145,33.50,53.25,55.50,53.00
2150,33.75,53.25,55.50,53.00
2155,
MAX31855K::SCV Fault: Thermocouple is shorted to VCC
53.50,55.50,53.00
2160,33.25,53.50,55.75,53.25
2165,33.50,53.50,55.75,53.25
2170,33.75,53.25,55.75,53.25
2175,
MAX31855K::SCG Fault: Thermocouple is shorted to GND
53.25,55.50,53.25
2180,
MAX31855K::SCV Fault: Thermocouple is shorted to VCC
53.50,55.75,53.25
2185,34.00,53.25,55.75,53.25
2190,
MAX31855K::SCV Fault: Thermocouple is shorted to VCC
53.50,55.75,53.25
2195,34.00,53.50,55.75,53.25
2200,33.50,53.50,55.75,53.25
2205,
MAX31855K::SCV Fault: Thermocouple is shorted to VCC
53.50,55.75,53.25
2210,34.00,53.25,55.75,53.25
2215,34.25,53.50,55.75,53.25
2220,34.00,53.50,55.75,53.50
2225,
MAX31855K::SCG Fault: Thermocouple is shorted to GND
53.50,56.00,53.25
2230,34.25,53.50,55.75,53.25
2235,34.25,53.50,55.75,53.25
2240,34.25,53.50,56.00,53.50
2245,34.00,53.50,56.00,53.50
2250,
MAX31855K::SCG Fault: Thermocouple is shorted to GND
53.50,56.00,53.50
2255,
MAX31855K::SCG Fault: Thermocouple is shorted to GND
53.75,56.00,53.50
2260,
MAX31855K::SCG Fault: Thermocouple is shorted to GND
53.75,56.00,53.50
2265,34.00,53.75,56.00,53.50
2270,
MAX31855K::SCV Fault: Thermocouple is shorted to VCC
53.75,56.00,53.50
2275,
MAX31855K::SCG Fault: Thermocouple is shorted to GND
53.75,56.00,53.50
2280,34.25,53.75,56.00,53.75
2285,34.50,53.75,56.00,53.75
2290,
MAX31855K::SCV Fault: Thermocouple is shorted to VCC
53.75,56.00,53.75
2295,34.25,53.75,56.00,53.75
2300,
MAX31855K::SCV Fault: Thermocouple is shorted to VCC
53.75,56.25,53.75
2305,34.50,53.75,56.00,53.75
2310,
MAX31855K::SCG Fault: Thermocouple is shorted to GND
54.00,56.25,53.75
2315,34.50,54.00,56.25,53.75
2320,34.50,54.00,56.25,53.75
2325,34.50,54.00,56.25,53.75
2330,34.50,54.00,56.25,53.75
2335,34.25,54.00,56.25,53.75
2340,
MAX31855K::SCV Fault: Thermocouple is shorted to VCC
54.00,56.25,53.75
2345,34.50,54.00,56.25,53.75
2350,
MAX31855K::SCG Fault: Thermocouple is shorted to GND
54.00,56.25,53.75
2355,34.75,54.00,56.25,54.00
2360,34.50,54.00,56.25,53.75
2365,
MAX31855K::SCG Fault: Thermocouple is shorted to GND
54.00,56.25,54.00
2370,
MAX31855K::SCG Fault: Thermocouple is shorted to GND
54.00,56.25,53.75
2375,34.50,54.00,56.25,54.00
2380,
MAX31855K::SCV Fault: Thermocouple is shorted to VCC
54.25,56.50,53.75
2385,
MAX31855K::SCG Fault: Thermocouple is shorted to GND
54.25,56.50,54.00
2390,
MAX31855K::SCG Fault: Thermocouple is shorted to GND
54.25,56.50,54.00
2395,
MAX31855K::SCG Fault: Thermocouple is shorted to GND
54.25,56.50,54.00
2400,35.00,54.25,56.50,54.00
2405,35.00,54.25,56.50,54.00
2410,35.00,54.25,56.50,54.00
2415,35.25,54.25,56.50,54.00
2420,
MAX31855K::SCV Fault: Thermocouple is shorted to VCC
54.25,56.50,54.00
2425,35.00,54.00,56.50,54.00
2430,35.25,54.25,56.50,54.00
2435,35.25,54.25,56.50,54.00
2440,35.00,54.25,56.50,54.00
2445,35.00,54.25,56.50,54.25
2450,35.25,54.25,56.75,54.25
2455,
MAX31855K::SCG Fault: Thermocouple is shorted to GND
54.25,56.75,54.00
2460,35.25,54.50,56.75,54.25
2465,
MAX31855K::SCV Fault: Thermocouple is shorted to VCC
54.25,56.75,54.25
2470,
MAX31855K::SCG Fault: Thermocouple is shorted to GND
54.50,56.75,54.25
2475,35.25,54.50,56.75,54.25
2480,35.00,54.50,56.75,54.25
2485,35.00,54.50,56.75,54.25
2490,
MAX31855K::SCG Fault: Thermocouple is shorted to GND
54.50,56.75,54.25
2495,35.00,54.50,56.75,54.25
2500,
MAX31855K::SCG Fault: Thermocouple is shorted to GND
54.50,56.75,54.50
2505,
MAX31855K::SCV Fault: Thermocouple is shorted to VCC
54.50,56.75,54.50
2510,35.00,54.50,57.00,54.50
2515,35.25,54.75,56.75,54.50
2520,
MAX31855K::SCG Fault: Thermocouple is shorted to GND
54.50,56.75,54.25
2525,35.25,54.75,57.00,54.50
2530,35.50,54.75,56.75,54.50
2535,
MAX31855K::SCG Fault: Thermocouple is shorted to GND
54.75,56.75,54.50
2540,
MAX31855K::SCG Fault: Thermocouple is shorted to GND
54.75,57.00,54.50
2545,35.50,54.50,56.75,54.50
2550,
MAX31855K::SCG Fault: Thermocouple is shorted to GND
54.75,57.00,54.50
2555,35.25,54.75,57.00,54.50
2560,35.50,54.75,57.00,54.50
2565,35.50,54.75,57.00,54.50
2570,35.50,54.75,57.00,54.50
2575,35.50,54.75,57.00,54.50
2580,35.50,54.75,57.00,54.75
2585,35.75,54.75,57.00,54.75
2590,
MAX31855K::SCV Fault: Thermocouple is shorted to VCC
54.75,57.00,54.75
2595,35.50,54.75,57.00,54.50
2600,35.75,54.75,57.00,54.75
2605,
MAX31855K::SCG Fault: Thermocouple is shorted to GND
54.75,57.25,54.75
2610,35.75,54.75,57.00,54.75
2615,35.75,54.75,57.25,54.75
2620,
MAX31855K::SCG Fault: Thermocouple is shorted to GND
54.75,57.25,54.75
2625,
MAX31855K::SCG Fault: Thermocouple is shorted to GND
55.00,57.00,54.75
2630,
MAX31855K::SCV Fault: Thermocouple is shorted to VCC
54.75,57.00,54.75
2635,
MAX31855K::SCG Fault: Thermocouple is shorted to GND
55.00,57.25,54.75
2640,35.75,54.75,57.25,54.75
2645,
MAX31855K::SCV Fault: Thermocouple is shorted to VCC
55.00,57.25,54.75
2650,35.75,55.00,57.25,55.00
2655,35.75,54.75,57.25,54.75
2660,36.00,55.00,57.25,54.75
2665,36.00,55.00,57.25,55.00
2670,36.00,55.00,57.25,55.00
2675,35.75,55.00,57.25,55.00
2680,36.25,55.00,57.25,55.00
2685,
MAX31855K::SCG Fault: Thermocouple is shorted to GND
55.00,57.50,55.00
2690,36.00,55.00,57.50,55.00
2695,
MAX31855K::SCG Fault: Thermocouple is shorted to GND
55.25,57.25,55.00
2700,
MAX31855K::SCV Fault: Thermocouple is shorted to VCC
55.00,57.50,55.00
2705,36.25,55.00,57.25,55.00
2710,
MAX31855K::SCG Fault: Thermocouple is shorted to GND
55.00,57.25,55.00
2715,36.00,55.00,57.50,55.00
2720,36.00,55.25,57.50,55.25
2725,
MAX31855K::SCV Fault: Thermocouple is shorted to VCC
55.25,57.50,55.00
2730,
MAX31855K::SCG Fault: Thermocouple is shorted to GND
55.00,57.50,55.00
2735,36.00,55.25,57.50,55.25
2740,36.00,55.25,57.50,55.25
2745,36.25,55.25,57.50,55.25
2750,36.25,55.25,57.75,55.25
2755,36.25,55.25,57.50,55.25
2760,36.00,55.25,57.50,55.25
2765,
MAX31855K::SCV Fault: Thermocouple is shorted to VCC
55.00,57.75,55.25
2770,36.25,55.00,57.75,55.25
2775,36.25,55.00,57.50,55.25
2780,36.25,55.00,57.50,55.25
2785,36.25,55.00,57.75,55.25
2790,
MAX31855K::SCG Fault: Thermocouple is shorted to GND
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

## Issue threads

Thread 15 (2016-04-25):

EMI hardening

marshalltaylorSFE, 2016-04-25:
Problem: Strong EM pulses can cause FTDI chip to lose the USB link until reset

Solution: Isolate FTDI ground such as in KTA-223v12.

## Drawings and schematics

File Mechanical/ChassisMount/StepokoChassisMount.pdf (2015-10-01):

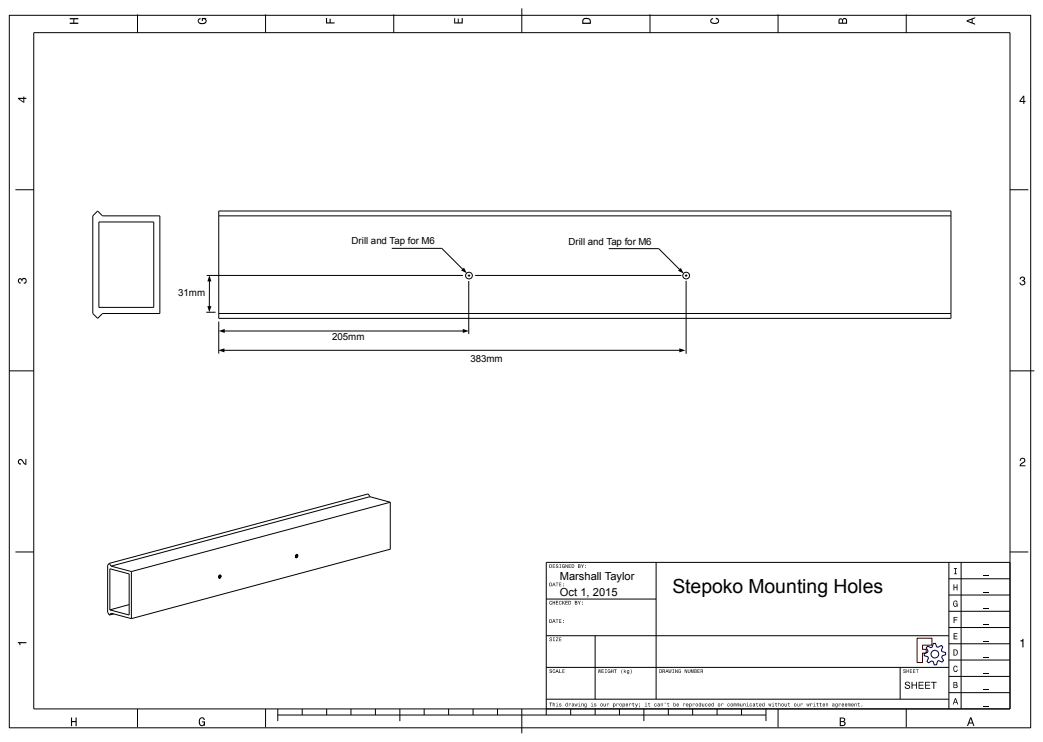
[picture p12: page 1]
Marshall Taylor; Oct 1, 2015; Stepoko Mounting Holes; Drill and Tap for M6

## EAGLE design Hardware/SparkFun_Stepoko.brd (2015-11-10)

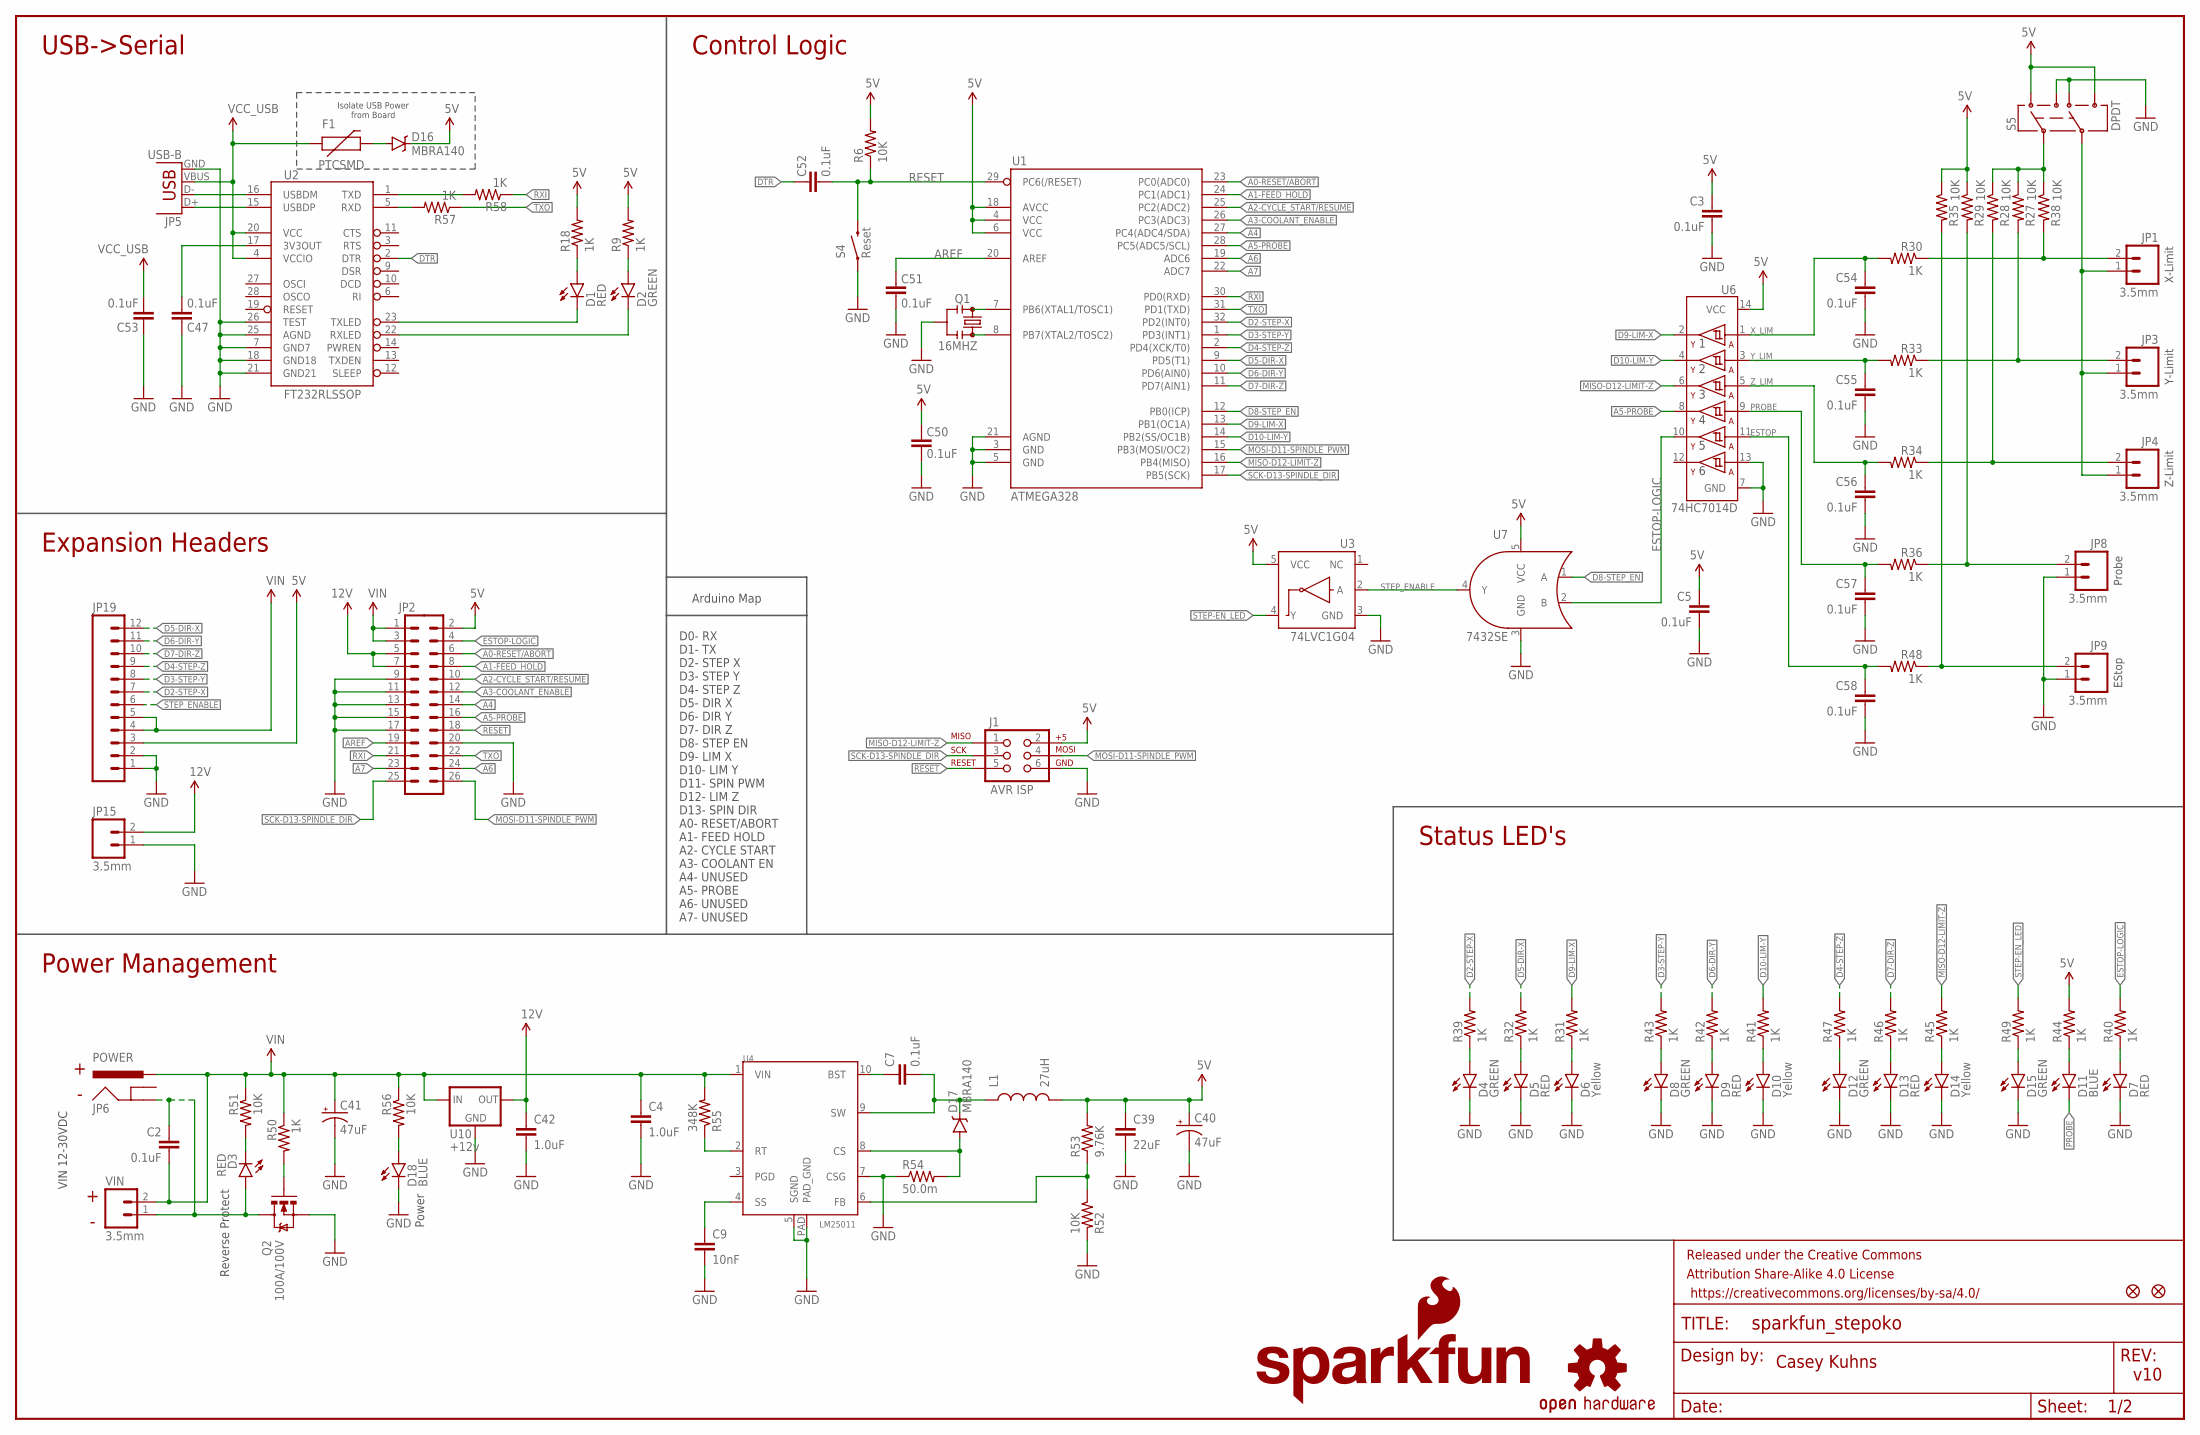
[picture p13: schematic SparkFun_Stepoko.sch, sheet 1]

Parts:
C2, C3, C5, C7, C47, C50, C51, C52, C53, C54, C55, C56, C57, C58: 0.1uF; 0603-CAP
C4, C42: 1.0uF; 1206-CAP
C9: 10nF; 0603-CAP
C39: 22uF; 1210
C40, C41: 47uF; PANASONIC_D
D1, D3, D5, D7, D9, D13: RED; LED-1206
D2, D4, D8, D12, D15: GREEN; LED-1206
D6, D10, D14: Yellow; LED-1206
D11, D18: BLUE; LED-1206
D16, D17: MBRA140; SMA-DIODE
F1: PTCSMD; PTC-1206
FID1, FID2: FIDUCIAL1X2; FIDUCIAL-1X2
FRAME1: FRAME-LEDGER; CREATIVE_COMMONS
J1: AVR ISP; 2X3
JP1, JP3, JP4, JP8, JP9, JP15: 3.5mm; SCREWTERMINAL-3.5MM-2_LOCK
JP2: M13X22X13; 2X13
JP5: USB-B; USB-B-PTH
JP6: POWER; POWER_JACK_PTH_LOCK
JP19: M12PTH; 1X12
L1: 27uH; INDUCTOR_SDR1307
LOGO1: OSHW-LOGOM; OSHW-LOGO-M
LOGO3: SFE_LOGO_NAME_FLAME.2_INCH; SFE_LOGO_NAME_FLAME_.2
Q1: 16MHZ; RESONATOR-SMD
Q2: 100A/100V; TO-263/D2PAK
R6, R27, R28, R29, R35, R38, R51, R52, R56: 10K; 0603-RES
R9, R18, R30, R33, R34, R36, R48, R50, R57, R58: 1K; 0603-RES@1
R31, R32, R39, R40, R41, R42, R43, R44, R45, R46, R47, R49: 1K; 0603-RES
R53: 9.76K; 0603
R54: 50.0m; 0603
R55: 348K; 0603
S4: Reset; TACTILE-SWITCH-SMD
S5: DPDT; AYZ0202
U1: ATMEGA328; TQFP32-08@1
U2: FT232RLSSOP; SSOP28DB
U3: 74LVC1G04; SOT353
U4: LM25011; HVSS0P-10
U6: 74HC7014D; SOIC-14
U7: 7432SE; SOT353
U10: +12v; TO-252
VIN: 3.5mm; SCREWTERMINAL-3.5MM-2_LOCK

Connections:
5V: C3.1, C5.1, C39.1, C40.+, C50.2, D16.C, J1.2, JP2.2, JP19.3, L1.P$2 (2), R6.2, R9.2, R18.2, R29.1, R35.1, R44.2, R53.2, S5.1, S5.6, U1.4 (VCC), U1.6 (VCC), U1.18 (AVCC), U3.5 (VCC), U6.14 (VCC), U7.5 (VCC); also elsewhere on the board
A0-RESET/ABORT: JP2.6, U1.23 (PC0(ADC0))
A1-FEED_HOLD: JP2.8, U1.24 (PC1(ADC1))
A2-CYCLE_START/RESUME: JP2.10, U1.25 (PC2(ADC2))
A3-COOLANT_ENABLE: JP2.12, U1.26 (PC3(ADC3))
A4: JP2.14, U1.27 (PC4(ADC4/SDA))
A5-PROBE: JP2.16, U1.28 (PC5(ADC5/SCL)), U6.8 (4Y)
A6: JP2.24, U1.19 (ADC6)
A7: JP2.23, U1.22 (ADC7)
AREF: C51.2, JP2.19, U1.20 (AREF)
D2-STEP-X: JP19.7, R39.2, U1.32 (PD2(INT0)); also elsewhere on the board
D3-STEP-Y: JP19.8, R43.2, U1.1 (PD3(INT1)); also elsewhere on the board
D4-STEP-Z: JP19.9, R47.2, U1.2 (PD4(XCK/T0)); also elsewhere on the board
D5-DIR-X: JP19.12, R32.2, U1.9 (PD5(T1)); also elsewhere on the board
D6-DIR-Y: JP19.11, R42.2, U1.10 (PD6(AIN0)); also elsewhere on the board
D7-DIR-Z: JP19.10, R46.2, U1.11 (PD7(AIN1)); also elsewhere on the board
D8-STEP_EN: U1.12 (PB0(ICP)), U7.1 (A)
D9-LIM-X: R31.2, U1.13 (PB1(OC1A)), U6.2 (1Y)
D10-LIM-Y: R41.2, U1.14 (PB2(SS/OC1B)), U6.4 (2Y)
D+: JP5.D+, U2.15 (USBDP)
D-: JP5.D-, U2.16 (USBDM)
DTR: C52.2, U2.2 (DTR)
ESTOP: C58.1, R48.2, U6.11 (5A)
ESTOP-LOGIC: JP2.4, R40.2, U6.10 (5Y), U7.2 (B)
GND: C3.2, C4.2, C5.2, C9.2, C39.2, C40.-, C41.-, C42.2, C47.2, C50.1, C51.1, C53.2, C54.2, C55.2, C56.2, C57.2, C58.2, D4.C, D5.C, D6.C, D7.C, D8.C, D9.C, D10.C, D12.C, D13.C, D14.C, D15.C, D18.C, J1.6, JP2.9, JP2.11, JP2.13, JP2.15, JP2.17, JP2.20, JP5.GND, JP8.1, JP9.1, JP15.1, JP19.1, JP19.2, Q1.2, Q2.3 (S), R52.2, R54.1, S4.1, S5.3, S5.4, U1.3 (GND), U1.5 (GND), U1.21 (AGND), U2.7 (GND7), U2.18 (GND18), U2.21 (GND21), U2.25 (AGND), U2.26 (TEST), U3.3 (GND), U4.5 (SGND), U4.7 (CSG), U4.PAD (PAD_GND), U6.7 (GND), U6.13 (6A), U7.3 (GND), U10.3 (GND); also elsewhere on the board
MISO-D12-LIMIT-Z: J1.1, R45.2, U1.16 (PB4(MISO)), U6.6 (3Y)
MOSI-D11-SPINDLE_PWM: J1.4, JP2.26, U1.15 (PB3(MOSI/OC2))
unnamed: R58.2, U2.1 (TXD)
unnamed: D2.A, R9.1
unnamed: D1.A, R18.1
unnamed: JP1.1, JP3.1, JP4.1, S5.5
unnamed: D7.A, R40.1
unnamed: Q1.3, U1.8 (PB7(XTAL2/TOSC2))
unnamed: JP1.2, R30.1, R38.2
unnamed: Q1.1, U1.7 (PB6(XTAL1/TOSC1))
unnamed: D11.A, R44.1
unnamed: D15.A, R49.1
unnamed: C2.1, D3.A, JP6.GND, Q2.2 (D), VIN.1
unnamed: D6.A, R31.1
unnamed: D5.A, R32.1
unnamed: D4.A, R39.1
unnamed: R52.1, R53.1, U4.6 (FB)
unnamed: D10.A, R41.1
unnamed: D9.A, R42.1
unnamed: D1.C, U2.23 (TXLED)
unnamed: D2.C, U2.22 (RXLED)
unnamed: D8.A, R43.1
unnamed: Q2.1 (G), R50.2
unnamed: D14.A, R45.1
unnamed: D3.C, R51.2
unnamed: JP3.2, R27.2, R33.1
unnamed: JP4.2, R28.2, R34.1
unnamed: D16.A, F1.2
unnamed: JP8.2, R29.2, R36.1
unnamed: JP9.2, R35.2, R48.1
unnamed: D18.A, R56.2
unnamed: D13.A, R46.1
unnamed: D12.A, R47.1
unnamed: R57.2, U2.5 (RXD)
unnamed: R55.1, U4.2 (RT)
unnamed: C7.1, U4.10 (BST)
unnamed: C7.2, D17.C, L1.P$1 (1), U4.9 (SW)
unnamed: C9.1, U4.4 (SS)
unnamed: R27.1, R28.1, R38.1, S5.2
unnamed: D17.A, R54.2, U4.8 (CS)
unnamed: C47.1, U2.17 (3V3OUT)
PROBE: C57.1, D11.C, R36.2, U6.9 (4A)
RESET: C52.1, J1.5, JP2.18, R6.1, S4.3 (2), U1.29 (PC6(/RESET))
RXI: JP2.21, R58.1, U1.30 (PD0(RXD))
SCK-D13-SPINDLE_DIR: J1.3, JP2.25, U1.17 (PB5(SCK))
STEP-EN_LED: R49.2, U3.4 (Y)
STEP_ENABLE: JP19.6, U3.2 (A), U7.4 (Y); also elsewhere on the board
TXO: JP2.22, R57.1, U1.31 (PD1(TXD))
VCC: C42.1, JP2.5, JP2.7, JP15.2, U10.2 (OUT)
VCC_USB: C53.1, F1.1, JP5.VBUS, U2.4 (VCCIO), U2.20 (VCC)
VIN: C2.2, C4.1, C41.+, JP2.1, JP2.3, JP6.PWR, JP19.4, JP19.5, R50.1, R51.1, R55.2, R56.1, U4.1 (VIN), U10.1 (IN), VIN.2; also elsewhere on the board
X_LIM: C54.1, R30.2, U6.1 (1A)
Y_LIM: C55.1, R33.2, U6.3 (2A)
Z_LIM: C56.1, R34.2, U6.5 (3A)

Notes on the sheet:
X-Limit
Y-Limit
Z-Limit
Probe
EStop
Isolate USB Power from Board
Status LED's
Power Management
Expansion Headers
USB->Serial
Control Logic
Reverse Protect
Power
Casey Kuhns
v10
D0- RX D1- TX D2- STEP X D3- STEP Y D4- STEP Z D5- DIR X D6- DIR Y D7- DIR Z D8- STEP EN D9- LIM X D10- LIM Y D11- SPIN PWM D12- LIM Z D13- SPIN DIR A0- RESET/ABORT A1- FEED HOLD A2- CYCLE START A3- COOLANT EN A4- UNUSED A5- PROBE A6- UNUSED A7- UNUSED
Arduino Map
VIN 12-30VDC

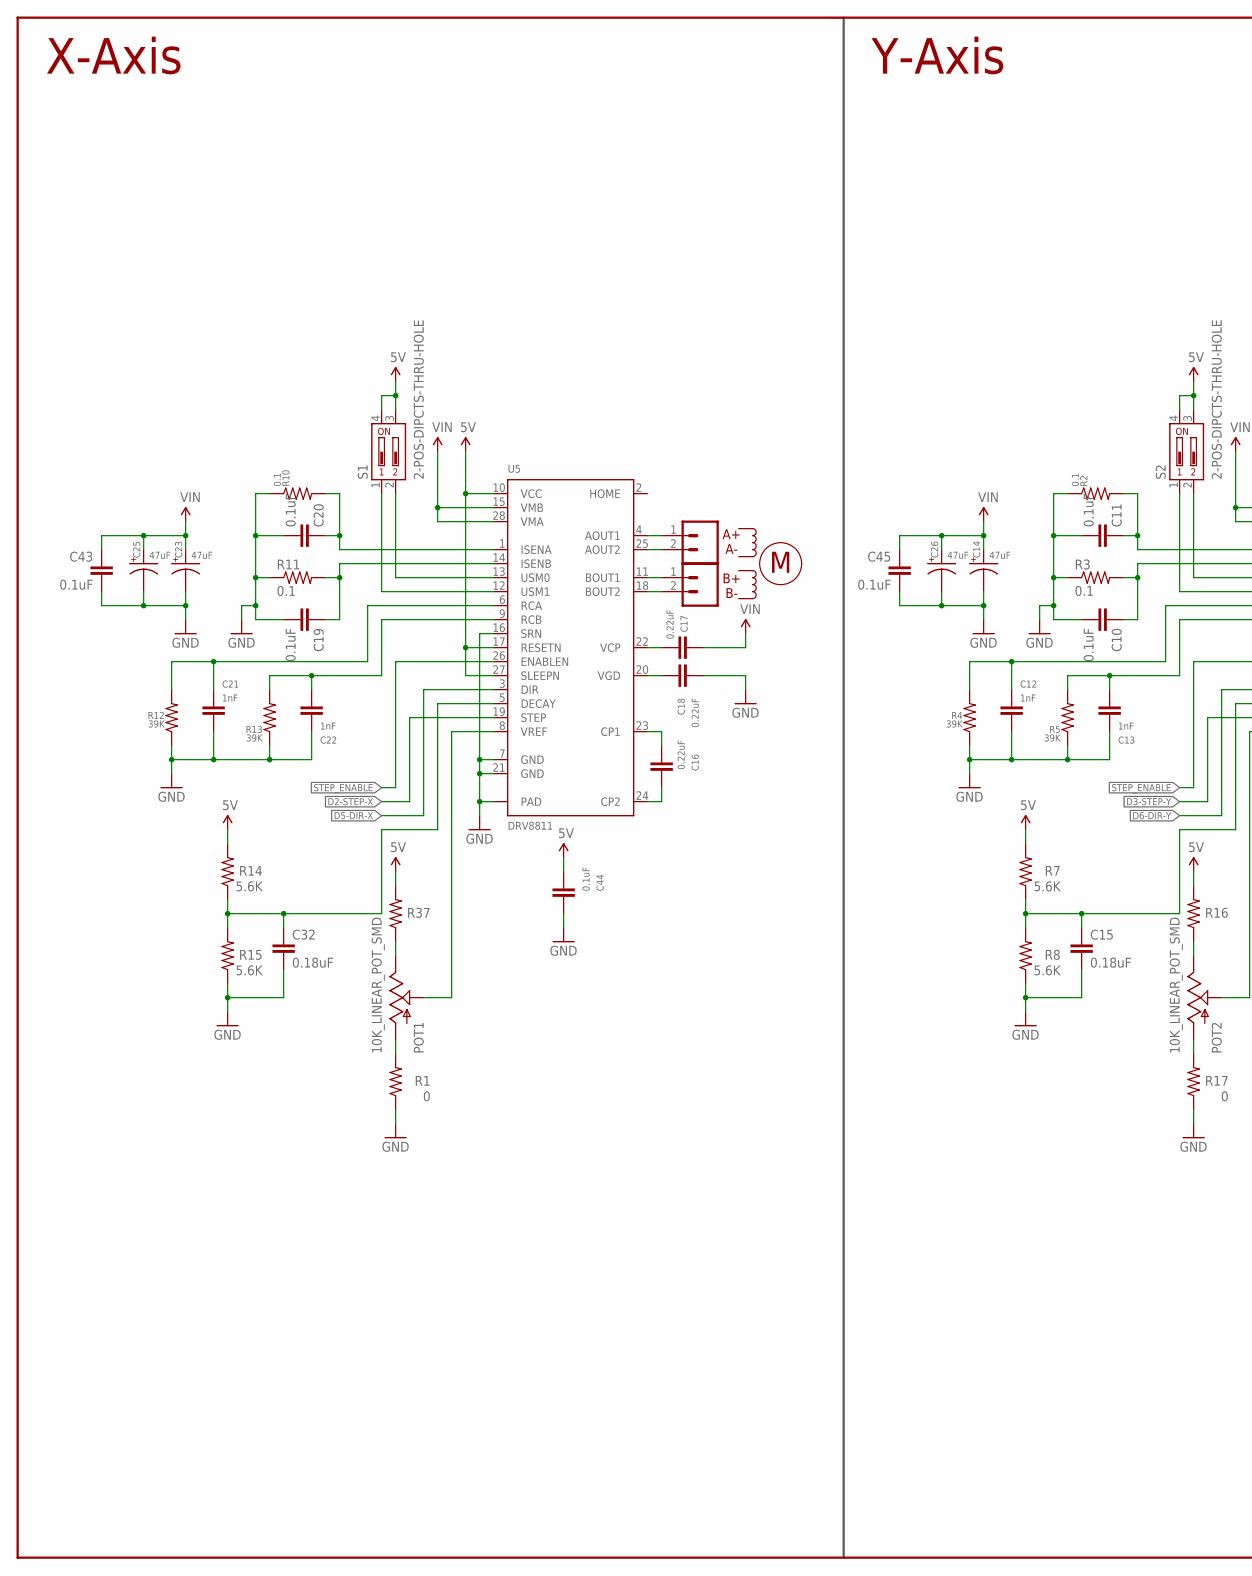
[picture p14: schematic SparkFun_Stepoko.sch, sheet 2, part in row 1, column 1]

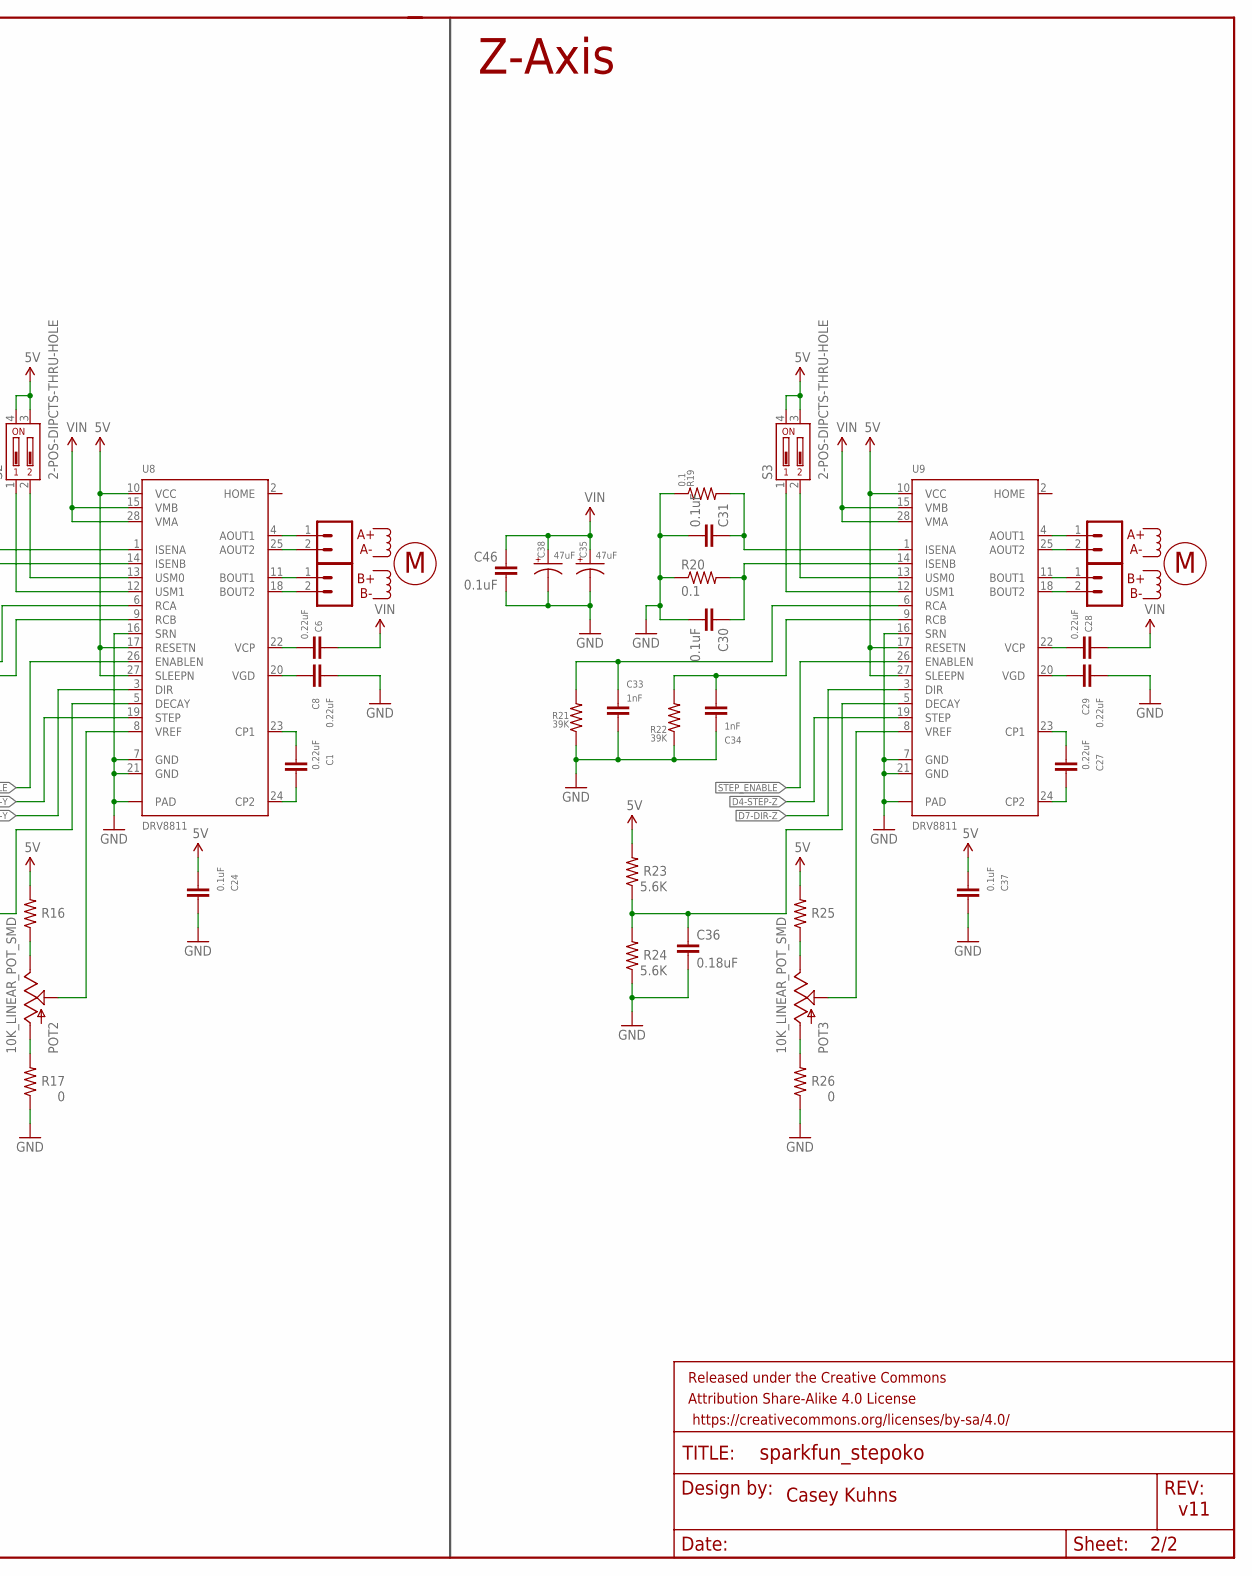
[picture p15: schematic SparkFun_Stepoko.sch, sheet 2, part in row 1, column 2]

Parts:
C1, C6, C8, C16, C17, C18, C27, C28, C29: 0.22uF; 0603-CAP
C10, C11, C19, C20, C24, C30, C31, C37, C43, C44, C45, C46: 0.1uF; 0603-CAP
C12, C13, C21, C22, C33, C34: 1nF; 0603-CAP
C14, C23, C25, C26, C35, C38: 47uF; PANASONIC_D
C15, C32, C36: 0.18uF; 0603
FRAME2: FRAME-LEDGER; CREATIVE_COMMONS
POT1, POT2, POT3: 10K_LINEAR_POT_SMD; TC33X
R1, R17, R26: 0; 0603
R2, R3, R10, R11, R19, R20: 0.1; 1210
R4, R5, R12, R13, R21, R22: 39K; 0603
R7, R8, R14, R15, R23, R24: 5.6K; 0603
R16, R25, R37: 10K; 0603-RES
S1, S2, S3: 2-POS-DIPCTS-THRU-HOLE; 209-2LPST
U5, U8, U9: DRV8811; HTSSOP28
X-A: 3.5mm; SCREWTERMINAL-3.5MM-2_LOCK
X-B: 3.5mm; SCREWTERMINAL-3.5MM-2_LOCK
Y-A: 3.5mm; SCREWTERMINAL-3.5MM-2_LOCK
Y-B: 3.5mm; SCREWTERMINAL-3.5MM-2_LOCK
Z-A: 3.5mm; SCREWTERMINAL-3.5MM-2_LOCK
Z-B: 3.5mm; SCREWTERMINAL-3.5MM-2_LOCK

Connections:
5V: C24.1, C37.1, C44.1, R7.2, R14.2, R16.2, R23.2, R25.2, R37.2, S1.3, S1.4, S2.3, S2.4, S3.3, S3.4, U5.10 (VCC), U5.17 (RESETN), U5.27 (SLEEPN), U8.10 (VCC), U8.17 (RESETN), U8.27 (SLEEPN), U9.10 (VCC), U9.17 (RESETN), U9.27 (SLEEPN); also elsewhere on the board
D2-STEP-X: U5.19 (STEP); also elsewhere on the board
D3-STEP-Y: U8.19 (STEP); also elsewhere on the board
D4-STEP-Z: U9.19 (STEP); also elsewhere on the board
D5-DIR-X: U5.3 (DIR); also elsewhere on the board
D6-DIR-Y: U8.3 (DIR); also elsewhere on the board
D7-DIR-Z: U9.3 (DIR); also elsewhere on the board
GND: C8.1, C10.2, C11.2, C12.2, C13.2, C14.-, C15.2, C18.1, C19.2, C20.2, C21.2, C22.2, C23.-, C24.2, C25.-, C26.-, C29.1, C30.2, C31.2, C32.2, C33.2, C34.2, C35.-, C36.2, C37.2, C38.-, C43.2, C44.2, C45.2, C46.2, R1.1, R2.1, R3.1, R4.1, R5.1, R8.1, R10.1, R11.1, R12.1, R13.1, R15.1, R17.1, R19.1, R20.1, R21.1, R22.1, R24.1, R26.1, U5.7 (GND), U5.16 (SRN), U5.21 (GND), U5.GND@10 (PAD), U5.GND@11 (PAD), U5.GND@12 (PAD), U5.GND@13 (PAD), U5.GND@14 (PAD), U5.GND@15 (PAD), U5.GND@16 (PAD), U5.GND@17 (PAD), U5.GND@18 (PAD), U5.GND@19 (PAD), U5.GND@20 (PAD), U5.GND@21 (PAD), U5.GND@22 (PAD), U5.GND@23 (PAD), U5.GND@24 (PAD), U5.GND@25 (PAD), U5.GND@26 (PAD), U5.GND@27 (PAD), U5.GND@28 (PAD), U5.GND@29 (PAD), U5.GND@30 (PAD), U5.GND@PAD (PAD), U8.7 (GND), U8.16 (SRN), U8.21 (GND), U8.GND@10 (PAD), U8.GND@11 (PAD), U8.GND@12 (PAD), U8.GND@13 (PAD), U8.GND@14 (PAD), U8.GND@15 (PAD), U8.GND@16 (PAD), U8.GND@17 (PAD), U8.GND@18 (PAD), U8.GND@19 (PAD), U8.GND@20 (PAD), U8.GND@21 (PAD), U8.GND@22 (PAD), U8.GND@23 (PAD), U8.GND@24 (PAD), U8.GND@25 (PAD), U8.GND@26 (PAD), U8.GND@27 (PAD), U8.GND@28 (PAD), U8.GND@29 (PAD), U8.GND@30 (PAD), U8.GND@PAD (PAD), U9.7 (GND), U9.16 (SRN), U9.21 (GND), U9.GND@10 (PAD), U9.GND@11 (PAD), U9.GND@12 (PAD), U9.GND@13 (PAD), U9.GND@14 (PAD), U9.GND@15 (PAD), U9.GND@16 (PAD), U9.GND@17 (PAD), U9.GND@18 (PAD), U9.GND@19 (PAD), U9.GND@20 (PAD), U9.GND@21 (PAD), U9.GND@22 (PAD), U9.GND@23 (PAD), U9.GND@24 (PAD), U9.GND@25 (PAD), U9.GND@26 (PAD), U9.GND@27 (PAD), U9.GND@28 (PAD), U9.GND@29 (PAD), U9.GND@30 (PAD), U9.GND@PAD (PAD); also elsewhere on the board
unnamed: POT1.3 (E), R37.1
unnamed: POT1.1 (A), R1.2
unnamed: C12.1, R4.2, U8.6 (RCA)
unnamed: C13.1, R5.2, U8.9 (RCB)
unnamed: C15.1, R7.1, R8.2, U8.5 (DECAY)
unnamed: S2.2, U8.13 (USM0)
unnamed: S2.1, U8.12 (USM1)
unnamed: C16.1, U5.24 (CP2)
unnamed: C16.2, U5.23 (CP1)
unnamed: C8.2, U8.20 (VGD)
unnamed: POT2.2 (S), U8.8 (VREF)
unnamed: C21.1, R12.2, U5.6 (RCA)
unnamed: C22.1, R13.2, U5.9 (RCB)
unnamed: C32.1, R14.1, R15.2, U5.5 (DECAY)
unnamed: S1.2, U5.13 (USM0)
unnamed: S1.1, U5.12 (USM1)
unnamed: U5.11 (BOUT1), X-B.1
unnamed: C18.2, U5.20 (VGD)
unnamed: POT2.3 (E), R16.1
unnamed: POT2.1 (A), R17.2
unnamed: C6.2, U8.22 (VCP)
unnamed: C1.1, U8.24 (CP2)
unnamed: C1.2, U8.23 (CP1)
unnamed: U8.11 (BOUT1), Y-B.1
unnamed: U8.18 (BOUT2), Y-B.2
unnamed: U8.4 (AOUT1), Y-A.1
unnamed: U8.25 (AOUT2), Y-A.2
unnamed: C10.1, R3.2, U8.14 (ISENB)
unnamed: C17.2, U5.22 (VCP)
unnamed: U5.18 (BOUT2), X-B.2
unnamed: U5.4 (AOUT1), X-A.1
unnamed: C11.1, R2.2, U8.1 (ISENA)
unnamed: C33.1, R21.2, U9.6 (RCA)
unnamed: C34.1, R22.2, U9.9 (RCB)
unnamed: C36.1, R23.1, R24.2, U9.5 (DECAY)
unnamed: S3.2, U9.13 (USM0)
unnamed: S3.1, U9.12 (USM1)
unnamed: U5.25 (AOUT2), X-A.2
unnamed: C29.2, U9.20 (VGD)
unnamed: POT3.2 (S), U9.8 (VREF)
unnamed: POT3.3 (E), R25.1
unnamed: POT3.1 (A), R26.2
unnamed: C28.2, U9.22 (VCP)
unnamed: C27.1, U9.24 (CP2)
unnamed: C27.2, U9.23 (CP1)
unnamed: U9.11 (BOUT1), Z-B.1
unnamed: U9.18 (BOUT2), Z-B.2
unnamed: U9.4 (AOUT1), Z-A.1
unnamed: U9.25 (AOUT2), Z-A.2
unnamed: C30.1, R20.2, U9.14 (ISENB)
unnamed: C19.1, R11.2, U5.14 (ISENB)
unnamed: C31.1, R19.2, U9.1 (ISENA)
unnamed: POT1.2 (S), U5.8 (VREF)
unnamed: C20.1, R10.2, U5.1 (ISENA)
STEP_ENABLE: U5.26 (ENABLEN), U8.26 (ENABLEN), U9.26 (ENABLEN); also elsewhere on the board
VIN: C6.1, C14.+, C17.1, C23.+, C25.+, C26.+, C28.1, C35.+, C38.+, C43.1, C45.1, C46.1, U5.15 (VMB), U5.28 (VMA), U8.15 (VMB), U8.28 (VMA), U9.15 (VMB), U9.28 (VMA); also elsewhere on the board

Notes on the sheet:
X-Axis
Y-Axis
Z-Axis
v11
Casey Kuhns
A+ A- B+ B-

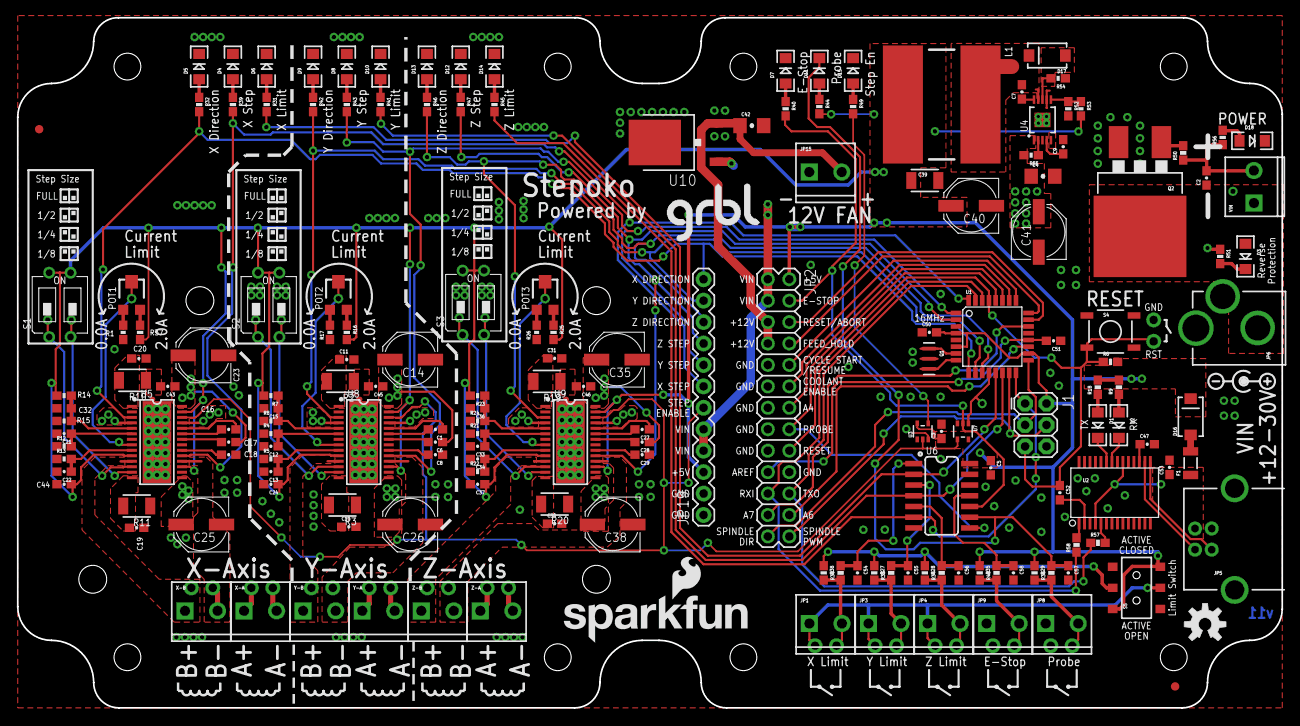
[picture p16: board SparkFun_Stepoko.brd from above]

Board: 2 copper layers, 149.9 x 81.8 mm, 184 parts (1 on the bottom side), 133 nets.

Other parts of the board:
LOGO2: SFE_LOGO_NAME_FLAME.2_INCH; SFE_LOGO_NAME_FLAME_.2@1
U$1: FLANGED_RED_ENCLOSURE-DIMENSION-NO-INNER-HOLES
U$2, U$3, U$4, U$5: STAND-OFF

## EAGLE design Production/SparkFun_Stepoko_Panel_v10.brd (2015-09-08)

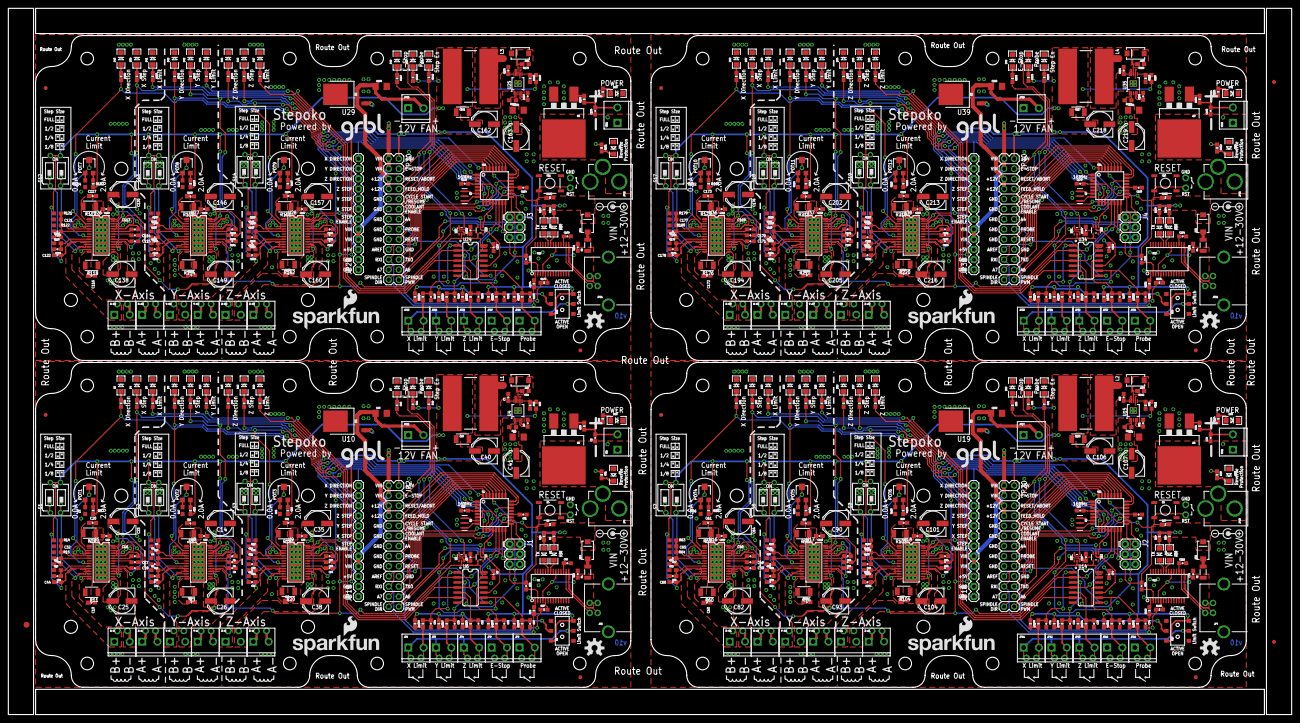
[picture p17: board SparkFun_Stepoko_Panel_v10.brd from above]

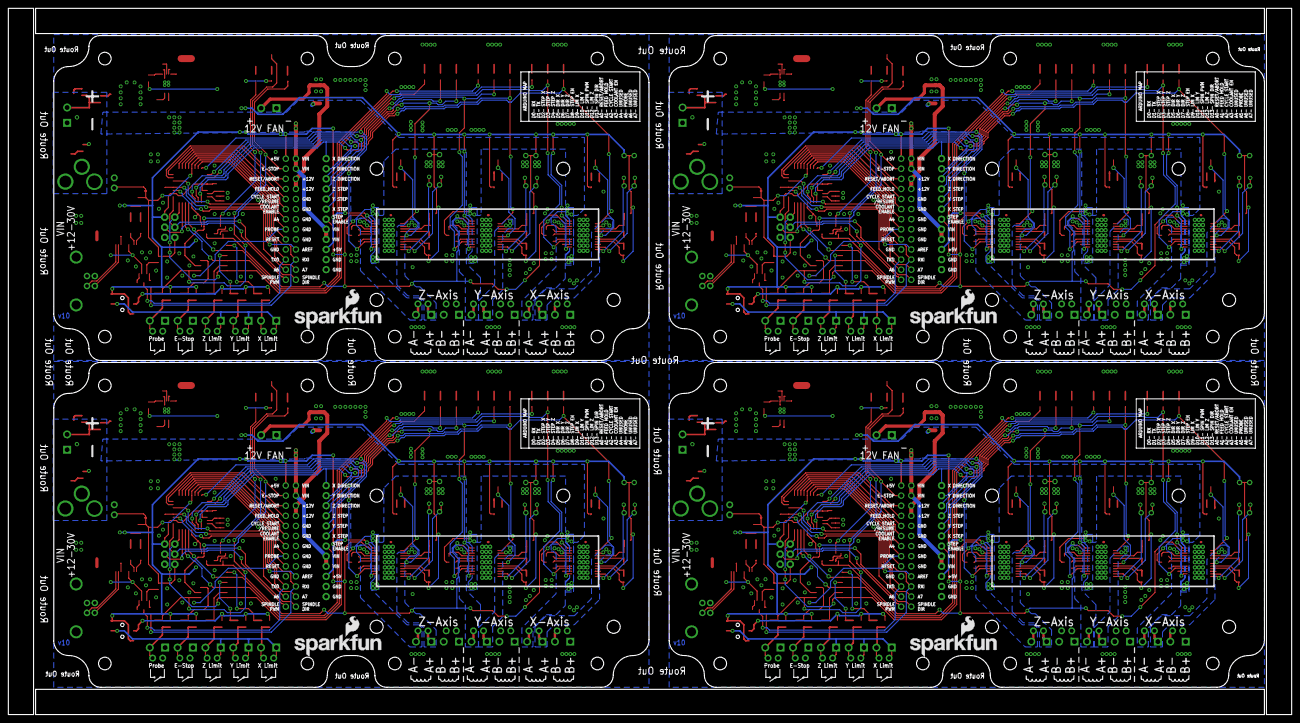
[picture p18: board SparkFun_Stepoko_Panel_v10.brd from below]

Board: 2 copper layers, 323.1 x 177.8 mm, 731 parts (4 on the bottom side), 532 nets.

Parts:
C1, C6, C8, C16, C17, C18, C27, C28, C29, C48, C49, C59, C83, C84, C85, C94, C95, C96, C113, C114, C115, C139, C140, C141, C150, C151, C152, C169, C170, C171, C195, C196, C197, C206, C207, C208: 0.22uF; 0603-CAP
C2, C3, C5, C7, C10, C11, C19, C20, C24, C30, C31, C37, C43, C44, C45, C46, C47, C50, C51, C52, C53, C54, C55, C56, C57, C58, C60, C61, C66, C67, C68, C69, C70, C71, C72, C73, C74, C75, C76, C77, C78, C80, C86, C87, C92, C97, C98, C103, C109, C110, C111, C112, C116, C117, C122, C123, C124, C125, C126, C127, C128, C129, C130, C131, C132, C133, C134, C136, C142, C143, C148, C153, C154, C159, C165, C166, C167, C168, C172, C173, C178, C179, C180, C181, C182, C183, C184, C185, C186, C187, C188, C189, C190, C192, C198, C199, C204, C209, C210, C215, C221, C222, C223, C224: 0.1uF; 0603-CAP
C4, C42, C79, C108, C135, C164, C191, C220: 1.0uF; 1206
C9, C81, C137, C193: 10nF; 0603-CAP
C12, C13, C21, C22, C33, C34, C62, C63, C88, C89, C99, C100, C118, C119, C144, C145, C155, C156, C174, C175, C200, C201, C211, C212: 1000pF; 0603-CAP
C14, C23, C25, C26, C35, C38, C40, C41, C64, C82, C90, C93, C101, C104, C106, C107, C120, C138, C146, C149, C157, C160, C162, C163, C176, C194, C202, C205, C213, C216, C218, C219: 47uF; PANASONIC_D
C15, C32, C36, C65, C91, C102, C121, C147, C158, C177, C203, C214: 0.18uF; 0603
C39, C105, C161, C217: 22uF; 1210
D1, D3, D5, D7, D9, D13, D19, D22, D25, D28, D30, D33, D37, D40, D43, D46, D48, D51, D55, D58, D61, D64, D66, D69: RED; LED-1206
D2, D4, D8, D12, D15, D20, D21, D24, D27, D32, D38, D39, D42, D45, D50, D56, D57, D60, D63, D68: GREEN; LED-1206
D6, D10, D14, D23, D26, D29, D41, D44, D47, D59, D62, D65: Yellow; LED-1206
D11, D18, D31, D35, D49, D53, D67, D71: BLUE; LED-1206
D16, D17, D34, D36, D52, D54, D70, D72: MBRA140; SMA-DIODE
E$1: FIDUCIAL-1.5X3
E$4, E$5: FIDUCIAL-1X2
F1, F2, F3, F4: PTCSMD; PTC-1206
FID1, FID2, FID3, FID4, FID5, FID6, FID7, FID8: FIDUCIAL1X2; FIDUCIAL-1X2
J1, J2, J3, J4: AVR ISP; 2X3
JP1, JP3, JP4, JP8, JP9, JP11, JP12, JP13, JP14, JP15, JP16, JP17, JP23, JP24, JP25, JP26, JP27, JP28, JP33, JP34, JP35, JP36, JP37, JP38: 3.5mm; SCREWTERMINAL-3.5MM-2_LOCK
JP2, JP20, JP30, JP40: 2X13
JP5, JP7, JP21, JP31: USB-B; USB-B-PTH
JP6, JP10, JP22, JP32: POWER; POWER_JACK_PTH_LOCK
JP18, JP19, JP29, JP39: 1X12
L1, L2, L3, L4: 27uH; INDUCTOR_SDR1307
LOGO1, LOGO4, LOGO7, LOGO10: OSHW-LOGOM; OSHW-LOGO-M
LOGO2, LOGO5, LOGO8, LOGO11: SFE_LOGO_NAME_FLAME.2_INCH; SFE_LOGO_NAME_FLAME_.2@1
LOGO3, LOGO6, LOGO9, LOGO12: SFE_LOGO_NAME_FLAME.2_INCH; SFE_LOGO_NAME_FLAME_.2
POT1, POT2, POT3, POT4, POT5, POT6, POT7, POT8, POT9, POT10, POT11, POT12: 2K_LINEAR_POT_SMD; TC33X
Q1, Q3, Q5, Q7: 16MHZ; RESONATOR-SMD
Q2, Q4, Q6, Q8: 100A/100V; TO-263/D2PAK
R1, R17, R26, R66, R102, R110, R124, R160, R168, R182, R218, R226: 0; 0603
R2, R3, R10, R11, R19, R20, R59, R60, R95, R96, R103, R104, R117, R118, R153, R154, R161, R162, R175, R176, R211, R212, R219, R220: 0.1; 1210
R4, R5, R12, R13, R21, R22, R61, R62, R97, R98, R105, R106, R119, R120, R155, R156, R163, R164, R177, R178, R213, R214, R221, R222: 39K; 0603
R6, R27, R28, R29, R35, R38, R51, R52, R56, R67, R70, R71, R72, R76, R78, R93, R94, R114, R125, R128, R129, R130, R134, R136, R151, R152, R172, R183, R186, R187, R188, R192, R194, R209, R210, R230: 10K; 0603-RES
R7, R8, R14, R15, R23, R24, R63, R64, R99, R100, R107, R108, R121, R122, R157, R158, R165, R166, R179, R180, R215, R216, R223, R224: 5.6K; 0603
R9, R18, R30, R31, R32, R33, R34, R36, R39, R40, R41, R42, R43, R44, R45, R46, R47, R48, R49, R50, R57, R58, R68, R69, R73, R74, R75, R77, R79, R80, R81, R82, R83, R84, R85, R86, R87, R88, R89, R90, R91, R92, R115, R116, R126, R127, R131, R132, R133, R135, R137, R138, R139, R140, R141, R142, R143, R144, R145, R146, R147, R148, R149, R150, R173, R174, R184, R185, R189, R190, R191, R193, R195, R196, R197, R198, R199, R200, R201, R202, R203, R204, R205, R206, R207, R208, R231, R232: 1K; 0603-RES
R16, R25, R37, R65, R101, R109, R123, R159, R167, R181, R217, R225: 3.3K; 0603-RES
R53, R111, R169, R227: 9.76K; 0603
R54, R112, R170, R228: 50.0m; 0603
R55, R113, R171, R229: 348K; 0603
S1, S2, S3, S7, S8, S9, S12, S13, S14, S17, S18, S19: 2-POS-DIPCTS-THRU-HOLE; 209-2LPST
S4, S6, S11, S16: Reset; TACTILE-SWITCH-SMD
S5, S10, S15, S20: DPDT; AYZ0202
U1, U11, U21, U31: ATMEGA328; TQFP32-08@1
U2, U12, U22, U32: FT232RLSSOP; SSOP28DB
U3, U20, U30, U40: 74LVC1G04; SOT353
U4, U15, U25, U35: LM25011; HVSS0P-10
U5, U8, U9, U16, U17, U18, U26, U27, U28, U36, U37, U38: DRV8811; HTSSOP28
U6, U14, U24, U34: 74HC7014D; SOIC-14
U7, U13, U23, U33: 7432SE; SOT353
U10, U19, U29, U39: +12v; TO-252
U$1, U$6, U$11, U$16: FLANGED_RED_ENCLOSURE-DIMENSION-NO-INNER-HOLES
U$2, U$3, U$4, U$5, U$7, U$8, U$9, U$10, U$12, U$13, U$14, U$15, U$17, U$18, U$19, U$20: STAND-OFF
VIN, VIN1, VIN2, VIN3: 3.5mm; SCREWTERMINAL-3.5MM-2_LOCK
X-A, X-A1, X-A2, X-A3: 3.5mm; SCREWTERMINAL-3.5MM-2_LOCK
X-B, X-B1, X-B2, X-B3: 3.5mm; SCREWTERMINAL-3.5MM-2_LOCK
Y-A, Y-A1, Y-A2, Y-A3: 3.5mm; SCREWTERMINAL-3.5MM-2_LOCK
Y-B, Y-B1, Y-B2, Y-B3: 3.5mm; SCREWTERMINAL-3.5MM-2_LOCK
Z-A, Z-A1, Z-A2, Z-A3: 3.5mm; SCREWTERMINAL-3.5MM-2_LOCK
Z-B, Z-B1, Z-B2, Z-B3: 3.5mm; SCREWTERMINAL-3.5MM-2_LOCK

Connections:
5V: C3.1, C5.1, C24.1, C37.1, C39.1, C40.+, C44.1, C50.2, D16.C, J1.2, JP2.2, JP19.3, L1.P$2, R6.2, R7.2, R9.2, R14.2, R16.2, R18.2, R23.2, R25.2, R29.1, R35.1, R37.2, R44.2, R53.2, S1.3, S1.4, S2.3, S2.4, S3.3, S3.4, S5.1, S5.6, U1.4, U1.6, U1.18, U3.5, U5.10, U5.17, U5.27, U6.14, U7.5, U8.10, U8.17, U8.27, U9.10, U9.17, U9.27
5V1: C66.1, C67.2, C76.1, C77.1, C92.1, C103.1, C105.1, C106.+, D36.C, J2.2, JP18.3, JP20.2, L2.P$2, R63.2, R65.2, R67.2, R68.2, R69.2, R72.1, R76.1, R90.2, R99.2, R101.2, R107.2, R109.2, R111.2, S7.3, S7.4, S8.3, S8.4, S9.3, S9.4, S10.1, S10.6, U11.4, U11.6, U11.18, U13.5, U14.14, U16.10, U16.17, U16.27, U17.10, U17.17, U17.27, U18.10, U18.17, U18.27, U20.5
5V2: C122.1, C123.2, C132.1, C133.1, C148.1, C159.1, C161.1, C162.+, D54.C, J3.2, JP29.3, JP30.2, L3.P$2, R121.2, R123.2, R125.2, R126.2, R127.2, R130.1, R134.1, R148.2, R157.2, R159.2, R165.2, R167.2, R169.2, S12.3, S12.4, S13.3, S13.4, S14.3, S14.4, S15.1, S15.6, U21.4, U21.6, U21.18, U23.5, U24.14, U26.10, U26.17, U26.27, U27.10, U27.17, U27.27, U28.10, U28.17, U28.27, U30.5
5V3: C178.1, C179.2, C188.1, C189.1, C204.1, C215.1, C217.1, C218.+, D72.C, J4.2, JP39.3, JP40.2, L4.P$2, R179.2, R181.2, R183.2, R184.2, R185.2, R188.1, R192.1, R206.2, R215.2, R217.2, R223.2, R225.2, R227.2, S17.3, S17.4, S18.3, S18.4, S19.3, S19.4, S20.1, S20.6, U31.4, U31.6, U31.18, U33.5, U34.14, U36.10, U36.17, U36.27, U37.10, U37.17, U37.27, U38.10, U38.17, U38.27, U40.5
A0-RESET/ABORT: JP2.6, U1.23
A0-RESET/ABORT1: JP20.6, U11.23
A0-RESET/ABORT2: JP30.6, U21.23
A0-RESET/ABORT3: JP40.6, U31.23
A1: JP20.14, U11.27
A1-FEED_HOLD: JP2.8, U1.24
A1-FEED_HOLD1: JP20.8, U11.24
A1-FEED_HOLD2: JP30.8, U21.24
A1-FEED_HOLD3: JP40.8, U31.24
A2: JP20.24, U11.19
A2-CYCLE_START/RESUME: JP2.10, U1.25
A2-CYCLE_START/RESUME1: JP20.10, U11.25
A2-CYCLE_START/RESUME2: JP30.10, U21.25
A2-CYCLE_START/RESUME3: JP40.10, U31.25
A3: JP20.23, U11.22
A3-COOLANT_ENABLE: JP2.12, U1.26
A3-COOLANT_ENABLE1: JP20.12, U11.26
A3-COOLANT_ENABLE2: JP30.12, U21.26
A3-COOLANT_ENABLE3: JP40.12, U31.26
A4: JP2.14, U1.27
A5: JP30.14, U21.27
A5-PROBE: JP2.16, U1.28, U6.8
A5-PROBE1: JP20.16, U11.28, U14.8
A5-PROBE2: JP30.16, U21.28, U24.8
A5-PROBE3: JP40.16, U31.28, U34.8
A6: JP2.24, U1.19
A7: JP2.23, U1.22
A8: JP30.24, U21.19
A9: JP30.23, U21.22
A10: JP40.14, U31.27
A11: JP40.24, U31.19
A12: JP40.23, U31.22
AREF: C51.2, JP2.19, U1.20
AREF1: C68.2, JP20.19, U11.20
AREF2: C124.2, JP30.19, U21.20
AREF3: C180.2, JP40.19, U31.20
D2-STEP-X: JP19.7, R39.2, U1.32, U5.19
D2-STEP-X1: JP18.7, R82.2, U11.32, U16.19
D2-STEP-X2: JP29.7, R140.2, U21.32, U26.19
D2-STEP-X3: JP39.7, R198.2, U31.32, U36.19
D3-STEP-Y: JP19.8, R43.2, U1.1, U8.19
D3-STEP-Y1: JP18.8, R85.2, U11.1, U17.19
D3-STEP-Y2: JP29.8, R143.2, U21.1, U27.19
D3-STEP-Y3: JP39.8, R201.2, U31.1, U37.19
D4-STEP-Z: JP19.9, R47.2, U1.2, U9.19
D4-STEP-Z1: JP18.9, R88.2, U11.2, U18.19
D4-STEP-Z2: JP29.9, R146.2, U21.2, U28.19
D4-STEP-Z3: JP39.9, R204.2, U31.2, U38.19
D5-DIR-X: JP19.12, R32.2, U1.9, U5.3
D5-DIR-X1: JP18.12, R81.2, U11.9, U16.3
D5-DIR-X2: JP29.12, R139.2, U21.9, U26.3
D5-DIR-X3: JP39.12, R197.2, U31.9, U36.3
D6-DIR-Y: JP19.11, R42.2, U1.10, U8.3
D6-DIR-Y1: JP18.11, R84.2, U11.10, U17.3
D6-DIR-Y2: JP29.11, R142.2, U21.10, U27.3
D6-DIR-Y3: JP39.11, R200.2, U31.10, U37.3
D7-DIR-Z: JP19.10, R46.2, U1.11, U9.3
D7-DIR-Z1: JP18.10, R87.2, U11.11, U18.3
D7-DIR-Z2: JP29.10, R145.2, U21.11, U28.3
D7-DIR-Z3: JP39.10, R203.2, U31.11, U38.3
D8-STEP_EN: U1.12, U7.1
D8-STEP_EN1: U11.12, U13.1
D8-STEP_EN2: U21.12, U23.1
D8-STEP_EN3: U31.12, U33.1
D9-LIM-X: R31.2, U1.13, U6.2
D9-LIM-X1: R80.2, U11.13, U14.2
D9-LIM-X2: R138.2, U21.13, U24.2
D9-LIM-X3: R196.2, U31.13, U34.2
D10-LIM-Y: R41.2, U1.14, U6.4
D10-LIM-Y1: R83.2, U11.14, U14.4
D10-LIM-Y2: R141.2, U21.14, U24.4
D10-LIM-Y3: R199.2, U31.14, U34.4
D+: JP5.D+, U2.15
D+1: JP7.D+, U12.15
D+2: JP21.D+, U22.15
D+3: JP31.D+, U32.15
D-: JP5.D-, U2.16
D-1: JP7.D-, U12.16
D-2: JP21.D-, U22.16
D-3: JP31.D-, U32.16
DTR: C52.2, U2.2
DTR1: C69.2, U12.2
DTR2: C125.2, U22.2
DTR3: C181.2, U32.2
ESTOP: C58.1, R48.2, U6.11
ESTOP1: C75.1, R79.2, U14.11
ESTOP2: C131.1, R137.2, U24.11
ESTOP3: C187.1, R195.2, U34.11
ESTOP-LOGIC: JP2.4, R40.2, U6.10, U7.2
ESTOP-LOGIC1: JP20.4, R89.2, U13.2, U14.10
ESTOP-LOGIC2: JP30.4, R147.2, U23.2, U24.10
ESTOP-LOGIC3: JP40.4, R205.2, U33.2, U34.10
GND: C3.2, C4.2, C5.2, C8.1, C9.2, C10.2, C11.2, C12.2, C13.2, C14.-, C15.2, C18.1, C19.2, C20.2, C21.2, C22.2, C23.-, C24.2, C25.-, C26.-, C29.1, C30.2, C31.2, C32.2, C33.2, C34.2, C35.-, C36.2, C37.2, C38.-, C39.2, C40.-, C41.-, C42.2, C43.2, C44.2, C45.2, C46.2, C47.2, C50.1, C51.1, C53.2, C54.2, C55.2, C56.2, C57.2, C58.2, D4.C, D5.C, D6.C, D7.C, D8.C, D9.C, D10.C, D12.C, D13.C, D14.C, D15.C, D18.C, J1.6, JP2.9, JP2.11, JP2.13, JP2.15, JP2.17, JP2.20, JP5.GND, JP8.1, JP9.1, JP15.1, JP19.1, JP19.2, Q1.2, Q2.3, R1.1, R2.1, R3.1, R4.1, R5.1, R8.1, R10.1, R11.1, R12.1, R13.1, R15.1, R17.1, R19.1, R20.1, R21.1, R22.1, R24.1, R26.1, R52.2, R54.1, S4.1, S5.3, S5.4, U1.3, U1.5, U1.21, U2.7, U2.18, U2.21, U2.25, U2.26, U3.3, U4.5, U4.7, U4.PAD, U5.7, U5.16, U5.21, U5.GND@10, U5.GND@11, U5.GND@12, U5.GND@13, U5.GND@14, U5.GND@15, U5.GND@16, U5.GND@17, U5.GND@18, U5.GND@19, U5.GND@20, U5.GND@21, U5.GND@22, U5.GND@23, U5.GND@24, U5.GND@25, U5.GND@26, U5.GND@27, U5.GND@28, U5.GND@29, U5.GND@30, U5.GND@PAD, U6.7, U6.13, U7.3, U8.7, U8.16, U8.21, U8.GND@10, U8.GND@11, U8.GND@12, U8.GND@13, U8.GND@14, U8.GND@15, U8.GND@16, U8.GND@17, U8.GND@18, U8.GND@19, U8.GND@20, U8.GND@21, U8.GND@22, U8.GND@23, U8.GND@24, U8.GND@25, U8.GND@26, U8.GND@27, U8.GND@28, U8.GND@29, U8.GND@30, U8.GND@PAD, U9.7, U9.16, U9.21, U9.GND@10, U9.GND@11, U9.GND@12, U9.GND@13, U9.GND@14, U9.GND@15, U9.GND@16, U9.GND@17, U9.GND@18, U9.GND@19, U9.GND@20, U9.GND@21, U9.GND@22, U9.GND@23, U9.GND@24, U9.GND@25, U9.GND@26, U9.GND@27, U9.GND@28, U9.GND@29, U9.GND@30, U9.GND@PAD, U10.3
GND1: C59.1, C60.2, C61.2, C62.2, C63.2, C64.-, C65.2, C66.2, C67.1, C68.1, C70.2, C71.2, C72.2, C73.2, C74.2, C75.2, C76.2, C77.2, C79.2, C81.2, C82.-, C85.1, C86.2, C87.2, C88.2, C89.2, C90.-, C91.2, C92.2, C93.-, C96.1, C97.2, C98.2, C99.2, C100.2, C101.-, C102.2, C103.2, C104.-, C105.2, C106.-, C107.-, C108.2, C109.2, C110.2, C111.2, C112.2, D21.C, D22.C, D23.C, D24.C, D25.C, D26.C, D27.C, D28.C, D29.C, D30.C, D32.C, D35.C, J2.6, JP7.GND, JP14.1, JP16.1, JP17.1, JP18.1, JP18.2, JP20.9, JP20.11, JP20.13, JP20.15, JP20.17, JP20.20, Q3.2, Q4.3, R59.1, R60.1, R61.1, R62.1, R64.1, R66.1, R94.2, R95.1, R96.1, R97.1, R98.1, R100.1, R102.1, R103.1, R104.1, R105.1, R106.1, R108.1, R110.1, R112.1, S6.1, S10.3, S10.4, U11.3, U11.5, U11.21, U12.7, U12.18, U12.21, U12.25, U12.26, U13.3, U14.7, U14.13, U15.5, U15.7, U15.PAD, U16.7, U16.16, U16.21, U16.GND@10, U16.GND@11, U16.GND@12, U16.GND@13, U16.GND@14, U16.GND@15, U16.GND@16, U16.GND@17, U16.GND@18, U16.GND@19, U16.GND@20, U16.GND@21, U16.GND@22, U16.GND@23, U16.GND@24, U16.GND@25, U16.GND@26, U16.GND@27, U16.GND@28, U16.GND@29, U16.GND@30, U16.GND@PAD, U17.7, U17.16, U17.21, U17.GND@10, U17.GND@11, U17.GND@12, U17.GND@13, U17.GND@14, U17.GND@15, U17.GND@16, U17.GND@17, U17.GND@18, U17.GND@19, U17.GND@20, U17.GND@21, U17.GND@22, U17.GND@23, U17.GND@24, U17.GND@25, U17.GND@26, U17.GND@27, U17.GND@28, U17.GND@29, U17.GND@30, U17.GND@PAD, U18.7, U18.16, U18.21, U18.GND@10, U18.GND@11, U18.GND@12, U18.GND@13, U18.GND@14, U18.GND@15, U18.GND@16, U18.GND@17, U18.GND@18, U18.GND@19, U18.GND@20, U18.GND@21, U18.GND@22, U18.GND@23, U18.GND@24, U18.GND@25, U18.GND@26, U18.GND@27, U18.GND@28, U18.GND@29, U18.GND@30, U18.GND@PAD, U19.3, U20.3
GND2: C115.1, C116.2, C117.2, C118.2, C119.2, C120.-, C121.2, C122.2, C123.1, C124.1, C126.2, C127.2, C128.2, C129.2, C130.2, C131.2, C132.2, C133.2, C135.2, C137.2, C138.-, C141.1, C142.2, C143.2, C144.2, C145.2, C146.-, C147.2, C148.2, C149.-, C152.1, C153.2, C154.2, C155.2, C156.2, C157.-, C158.2, C159.2, C160.-, C161.2, C162.-, C163.-, C164.2, C165.2, C166.2, C167.2, C168.2, D39.C, D40.C, D41.C, D42.C, D43.C, D44.C, D45.C, D46.C, D47.C, D48.C, D50.C, D53.C, J3.6, JP21.GND, JP26.1, JP27.1, JP28.1, JP29.1, JP29.2, JP30.9, JP30.11, JP30.13, JP30.15, JP30.17, JP30.20, Q5.2, Q6.3, R117.1, R118.1, R119.1, R120.1, R122.1, R124.1, R152.2, R153.1, R154.1, R155.1, R156.1, R158.1, R160.1, R161.1, R162.1, R163.1, R164.1, R166.1, R168.1, R170.1, S11.1, S15.3, S15.4, U21.3, U21.5, U21.21, U22.7, U22.18, U22.21, U22.25, U22.26, U23.3, U24.7, U24.13, U25.5, U25.7, U25.PAD, U26.7, U26.16, U26.21, U26.GND@10, U26.GND@11, U26.GND@12, U26.GND@13, U26.GND@14, U26.GND@15, U26.GND@16, U26.GND@17, U26.GND@18, U26.GND@19, U26.GND@20, U26.GND@21, U26.GND@22, U26.GND@23, U26.GND@24, U26.GND@25, U26.GND@26, U26.GND@27, U26.GND@28, U26.GND@29, U26.GND@30, U26.GND@PAD, U27.7, U27.16, U27.21, U27.GND@10, U27.GND@11, U27.GND@12, U27.GND@13, U27.GND@14, U27.GND@15, U27.GND@16, U27.GND@17, U27.GND@18, U27.GND@19, U27.GND@20, U27.GND@21, U27.GND@22, U27.GND@23, U27.GND@24, U27.GND@25, U27.GND@26, U27.GND@27, U27.GND@28, U27.GND@29, U27.GND@30, U27.GND@PAD, U28.7, U28.16, U28.21, U28.GND@10, U28.GND@11, U28.GND@12, U28.GND@13, U28.GND@14, U28.GND@15, U28.GND@16, U28.GND@17, U28.GND@18, U28.GND@19, U28.GND@20, U28.GND@21, U28.GND@22, U28.GND@23, U28.GND@24, U28.GND@25, U28.GND@26, U28.GND@27, U28.GND@28, U28.GND@29, U28.GND@30, U28.GND@PAD, U29.3, U30.3
GND3: C171.1, C172.2, C173.2, C174.2, C175.2, C176.-, C177.2, C178.2, C179.1, C180.1, C182.2, C183.2, C184.2, C185.2, C186.2, C187.2, C188.2, C189.2, C191.2, C193.2, C194.-, C197.1, C198.2, C199.2, C200.2, C201.2, C202.-, C203.2, C204.2, C205.-, C208.1, C209.2, C210.2, C211.2, C212.2, C213.-, C214.2, C215.2, C216.-, C217.2, C218.-, C219.-, C220.2, C221.2, C222.2, C223.2, C224.2, D57.C, D58.C, D59.C, D60.C, D61.C, D62.C, D63.C, D64.C, D65.C, D66.C, D68.C, D71.C, J4.6, JP31.GND, JP36.1, JP37.1, JP38.1, JP39.1, JP39.2, JP40.9, JP40.11, JP40.13, JP40.15, JP40.17, JP40.20, Q7.2, Q8.3, R175.1, R176.1, R177.1, R178.1, R180.1, R182.1, R210.2, R211.1, R212.1, R213.1, R214.1, R216.1, R218.1, R219.1, R220.1, R221.1, R222.1, R224.1, R226.1, R228.1, S16.1, S20.3, S20.4, U31.3, U31.5, U31.21, U32.7, U32.18, U32.21, U32.25, U32.26, U33.3, U34.7, U34.13, U35.5, U35.7, U35.PAD, U36.7, U36.16, U36.21, U36.GND@10, U36.GND@11, U36.GND@12, U36.GND@13, U36.GND@14, U36.GND@15, U36.GND@16, U36.GND@17, U36.GND@18, U36.GND@19, U36.GND@20, U36.GND@21, U36.GND@22, U36.GND@23, U36.GND@24, U36.GND@25, U36.GND@26, U36.GND@27, U36.GND@28, U36.GND@29, U36.GND@30, U36.GND@PAD, U37.7, U37.16, U37.21, U37.GND@10, U37.GND@11, U37.GND@12, U37.GND@13, U37.GND@14, U37.GND@15, U37.GND@16, U37.GND@17, U37.GND@18, U37.GND@19, U37.GND@20, U37.GND@21, U37.GND@22, U37.GND@23, U37.GND@24, U37.GND@25, U37.GND@26, U37.GND@27, U37.GND@28, U37.GND@29, U37.GND@30, U37.GND@PAD, U38.7, U38.16, U38.21, U38.GND@10, U38.GND@11, U38.GND@12, U38.GND@13, U38.GND@14, U38.GND@15, U38.GND@16, U38.GND@17, U38.GND@18, U38.GND@19, U38.GND@20, U38.GND@21, U38.GND@22, U38.GND@23, U38.GND@24, U38.GND@25, U38.GND@26, U38.GND@27, U38.GND@28, U38.GND@29, U38.GND@30, U38.GND@PAD, U39.3, U40.3
MISO-D12-LIMIT-Z: J1.1, R45.2, U1.16, U6.6
MISO-D12-LIMIT-Z1: J2.1, R86.2, U11.16, U14.6
MISO-D12-LIMIT-Z2: J3.1, R144.2, U21.16, U24.6
MISO-D12-LIMIT-Z3: J4.1, R202.2, U31.16, U34.6
MOSI-D11-SPINDLE_PWM: J1.4, JP2.26, U1.15
MOSI-D11-SPINDLE_PWM1: J2.4, JP20.26, U11.15
MOSI-D11-SPINDLE_PWM2: J3.4, JP30.26, U21.15
MOSI-D11-SPINDLE_PWM3: J4.4, JP40.26, U31.15
unnamed: R58.2, U2.1
unnamed: D2.A, R9.1
unnamed: D1.A, R18.1
unnamed: JP1.1, JP3.1, JP4.1, S5.5
unnamed: D7.A, R40.1
unnamed: Q1.3, U1.8
unnamed: JP1.2, R30.1, R38.2
unnamed: Q1.1, U1.7
unnamed: POT1.3, R37.1
unnamed: POT1.1, R1.2
unnamed: C12.1, R4.2, U8.6
unnamed: C13.1, R5.2, U8.9
unnamed: D11.A, R44.1
unnamed: C15.1, R7.1, R8.2, U8.5
unnamed: S2.2, U8.13
unnamed: D15.A, R49.1
unnamed: C2.1, D3.A, JP6.GND, Q2.2, VIN.1
unnamed: D6.A, R31.1
unnamed: D5.A, R32.1
unnamed: D4.A, R39.1
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

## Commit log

2015-02-05 initial commit for v2 of GRBL Board
    [GRBLShieldv2.brd, GRBLShieldv2.sch]
2015-02-05 schematic cleanup
    [GRBLShieldv2.brd, GRBLShieldv2.sch]
2015-02-06 more cleanup
    [GRBLShieldv2.brd, GRBLShieldv2.sch]
2015-02-06 renamed board and continued cleanup
    [Stepoko.brd, Stepoko.sch]
2015-02-08 revision changes from review
    [Stepoko.brd, Stepoko.sch]
2015-02-08 made changes from design review
    [Stepoko.brd, Stepoko.sch]
2015-02-08 added prod-ids
    [Stepoko.brd, Stepoko.sch]
2015-02-08 name change
    [SparkFun_Stepoko.brd, SparkFun_Stepoko.sch]
2015-02-09 fixed all issued in github
    [SparkFun_Stepoko.brd, SparkFun_Stepoko.sch]
2015-02-09 changes made from github
    [SparkFun_Stepoko.brd, SparkFun_Stepoko.sch]
2015-03-02 making changes for second proto round
    [SparkFun_Stepoko.brd, SparkFun_Stepoko.sch]
2015-03-03 finished modifications from proto review
    [SparkFun_Stepoko.brd, SparkFun_Stepoko.sch]
2015-03-04 made changes and added logos. Added test points
    [SparkFun_Stepoko.brd, SparkFun_Stepoko.sch]
2015-03-04 made changes from issues in repo
    [SparkFun_Stepoko.brd, SparkFun_Stepoko.sch]
2015-04-27 fixing high impedance issues
    [SparkFun_Stepoko.brd, SparkFun_Stepoko.sch]
2015-04-28 enlarged stepper traces and improved Ground Planes
    [SparkFun_Stepoko.brd]
2015-04-28 moving components for ground pours
    [SparkFun_Stepoko.brd]
2015-04-29 more work on power planes
    [SparkFun_Stepoko.brd]
2015-05-01 Testing Assembly Variants
    [SparkFun_Stepoko.brd, SparkFun_Stepoko.sch]
2015-05-04 adding room for heatsinks
    [SparkFun_Stepoko.brd, SparkFun_Stepoko.sch]
2015-05-11 updated version numbers
    [SparkFun_Stepoko.brd, SparkFun_Stepoko.sch]
2015-05-13 fixed designed by placement
    [SparkFun_Stepoko.brd]
2015-05-14 found via hitting trace
    [SparkFun_Stepoko.brd]
2015-05-14 corrected issues in github
    [SparkFun_Stepoko.brd, SparkFun_Stepoko.sch]
2015-06-29 Corrected Probe functionality and updated silk to better reflect limit switch functionality, moved Arduino table to better fit board layout
    [SparkFun_Stepoko.brd, SparkFun_Stepoko.sch]
2015-07-01 corrected issued from Design review. Opened up holes to prevent potential shorts, schematic cleanup.
    [SparkFun_Stepoko.brd, SparkFun_Stepoko.sch]
2015-07-01 updated version number
    [SparkFun_Stepoko.brd, SparkFun_Stepoko.sch]
2015-07-01 fixed current limit resistor values
    [SparkFun_Stepoko.brd, SparkFun_Stepoko.sch]
2015-07-07 added test points to current limit resistors
    [SparkFun_Stepoko.brd]
2015-07-07 moved dimensions to fit with .01 grid
    [SparkFun_Stepoko.brd, SparkFun_Stepoko.sch]
2015-07-07 created panel v10
    [SparkFun_Stepoko_Panel_v10.brd]
2015-09-08 added heatsink design files
    [HeatSink.SLDPRT, HeatSinkJig.SLDASM, JigBase.SLDPRT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]
2015-09-27 added g-code
    [Components.FCStd, freecadexport.dxf, panel_holes.dxf]
2015-09-27 Ready for fab
    [BackPart.FCStd, BackPart.dxf, BottomPart.FCStd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]
2015-10-01 moving along on testing
    [ConfiguringYAxis.txt, FrontPart.FCStd, FrontPart.dxf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]
2015-10-01 updated current drive setting resistors
    [SparkFun_Stepoko.brd, SparkFun_Stepoko.sch]
2015-10-01 added readme and updated to v11 hardware
    [SparkFun_Stepoko.brd, SparkFun_Stepoko.sch]
2015-11-02 added part docu
    [RailPart.FCStd]
2015-11-10 Added notes folder
    [Product chart (Dry-erase board).ods]
2015-11-10 Replaced 25v cap with 100v cap
    [SparkFun_Stepoko.brd, SparkFun_Stepoko.sch]
2015-11-16 re-arranged example folders
    [BackPart.FCStd, BackPart.dxf, BottomPart.FCStd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]
2015-11-20 Finalized documentation
    [Product chart (Dry-erase board).ods]

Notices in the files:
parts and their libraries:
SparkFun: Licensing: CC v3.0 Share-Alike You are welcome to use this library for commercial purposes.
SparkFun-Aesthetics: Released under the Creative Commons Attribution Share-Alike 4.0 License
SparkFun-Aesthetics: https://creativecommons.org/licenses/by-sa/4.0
